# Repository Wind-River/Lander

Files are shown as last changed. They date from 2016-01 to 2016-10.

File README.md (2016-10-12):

### Overview

We will present a physical interactive model of the famous LEM Lander game, where the user attempts to land a Rocket model (suspended from a four tower cable system) that has limited fuel onto a crater-filled lunar surface.  The game has outputs to indicate the speed, altitude, and fuel level remaining, together with light and sound effects. There will be physical controller inputs for the thrust and direction, plus controls for the game play.

### Project License

The license for this project is the Apache-2.0. Text of Apache-2.0 license and other applicable license notices can be found in the LICENSE-NOTICES.txt file in the top level directory. Each source files should include a license notice that designates the licensing terms for the respective file.

### Legal Notices

Disclaimer of Warranty / No Support: Wind River does not provide support and maintenance services for this software, under Wind River’s standard Software Support and Maintenance Agreement or otherwise. Unless required by applicable law, Wind River provides the software (and each contributor provides its contribution) on an “AS IS” BASIS, WITHOUT WARRANTIES OF ANY KIND, either express or implied, including, without limitation, any warranties of TITLE, NONINFRINGEMENT, MERCHANTABILITY, or FITNESS FOR A PARTICULAR PURPOSE. You are solely responsible for determining the appropriateness of using or redistributing the software and assume ay risks associated with your exercise of permissions under the license.

### Materials Used

 * Galileo Rev2 running the Rocket (Zephyr) OS
 * Two Arduino Coprocessors 
 * 4 Stepper Motors and Drivers 
 * I2C LCD Display
 * I2C LED Large Display
 * 2 TM1637 LED Displays
 * Audio FX Sound Board
 * Pan and Tilt mount with 2 servo motors
 * Digital RGB LED Strip
 * Arcade Joystick, Buttons, and Slider Controls
 * AC power for a power strip connection
 * An internet connection (for Helix Application Cloud)
 * W=28”, D=20”, H=24” play field

### Software Used

  * Wind River Helix Application Cloud (HAC), open registration
    * http://app.cloud.windriver.com
  * Helix Application Cloud, sample application "Grove-LCD"

#### CAD and STL

  * All STL files are located in the /cad directory
  * CAD drawings for the Lander are available at - https://cad.onshape.com/documents/7df8b4dcfbc827b905a6e076

### Installation

  * Set up a free Wind River Helix Application Cloud (HAC) account (https://app.cloud.windriver.com)
  * Download the card image for the Galileo from HAC, write it to a microSD card, and insert into the Galileo
  * Create a new "Rocket_Lander" project in HAC, using the "Grove-LCD" sample application as the base
  * Set up a Galilieo Rev2 board with the following hardware:
    * A Seeed Studio Grove base shield
    * A Seeed Studio Grove button to D3
    * A Seeed Studio Grove button to D7
    * A Seeed Studio Grove LCD module to I2C
    * An FTDI cable to your host
  * Boot the Galileo, download the "Rocket_Lander" project, and do a test run with this initial application
  * Follow the Frizting diagram to attach the remaining hardware, for example:
     * The joystick cable to A0
     * The rheostat slider to A3
     * A Seeed Studio Grove PWM splitter cable from D5 to the pan and tilt stage
     * A Seeed Studio Grove breakout cable from I2C to the Adafruit I2C LED backpack
     * A Seeed Studio Grove cable with +5v cut from I2C to each of the the satellite boards
  * Follow the Frizting diagram to construct the motor driver circuit board 
  * Add code from the "source/firmware" to the "Rocket_Lander" project
  * Add code from the "source/satelliteware/libraries" to Arduino libraries directory
  * Set up the Rocket Display Arduino board
    * Install code from the "source/satelliteware/rocket_display"
    * Attach the two Seeed Studio Grove LED displays
    * Attach the Seeed Studio Grove Chainable RGB LED
    * Attach the Adafruit sound board
  * Set up the Rocket Motor Arduino board
    * Install code from the "source/satelliteware/rocket_motor"
    * Connect to the motor driver circuit board
  * Assemble the play field with the towers, stepper motors, fish line cables, and the model rocket:
    * cut a board to 28 inches by 22 inches for the playing field
    * cut four 1/2 inch square aluminum rods to 24 inches, to be the line towers
    * 3D print the four rod/motor mounts, and install on the playing field at 24 inches by 18 inches
    * 3D print the four spool cylinders and attach to the stepper motors
    * 3D print the four line rollers, and install at the top of the four towers
    * 3D print the rocket model, or provide a desired alternative
    * cut four lenghts of fish line to be the line cable, to about 60 inches
    * attach each of the four cable lines from each of the spools to the respective rocket model corner
    * attach the pan and tilt stage
    * connect the motor driver board to the stepper motors
  * Power the system, run the full "Rocket_Lander" project from HAC, follow the play instructions on the LED display interface

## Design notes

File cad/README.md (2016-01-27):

# CAD
This section will provide all physical designed files

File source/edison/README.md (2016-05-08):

#Edison Board Set up

 * To set up the board
 ```
 configure_edison --setup
 ```
 * Copy Contents of this edision directory to /home/root on the edison board
 * Install python libraries pyserial and requests
```
pip install pyserial
pip install requests
```
 * Copy startup script to /etc/init.d/rocketLanderStart
 * Put rocketLanderStart in startup with 
 ```
update-rc.d -f rocketLanderStart defaults
 ```

 * Setup Complete

##Wifi
 * Will need to be reconfigured, atm only works at WIND 
 * configure_edison --wifi

##Bluetooth
 * Will show up as RocketLander in bluetooth list
 * Default bluetooth pin is 0505
 * Set up to start up automatically

##Arduino to Edison Serial
 * Set up to start up automatically
 * log file at /home/root/arduino_edison.log
 * User DEBUG  flag to send mock data back and forth. MEAN.io rest api call is not called.
```
 python arduino_edison.py DEBUG
 ```
 * Submit High Score Message and Reply
```
a2e:name=______,score=______;
e2a:ack;
```
 * Get HighScore Message and Reply
```
a2e:highscore?;
e2a:name=_____,score=______;
```

##Rest Api Calls
 * rocketLanderRest.py calls mean stack rest api. If host changes, change ipaddress here
 * a no args equals a get for high scorre, the first 5 is returned
 * pass a json string for submit. primary key is email address
```
    [{
        "email": "mojo3@jupiter.com",
        "lander_score": 999,
        "name": "Mojo Doggie 3",
        "phone": "555-555-5555",
        "reference": "510-749-2000"
    }]
```

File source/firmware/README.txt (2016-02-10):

1) Introduction

This is the source code for the Rocket Lander main board, the Galileo.

2) Board Bring Up

  (a) Setup the Galileo with a Grove LCD on I2C and a Grove button on D3

  (b) Get the Grove-LCD sample Helix Application running
  
This will show that Rocket is working with the miniaml I/O.

  (c1) Setup the Rocket_Lander project in Helix
  
  (c2) Add these components to the Galieo
     * A Grove button on D7
     * The joystick cable to A0
     * The slider cable to A3
     * A Grove PWM splitter cable from D5 to the pan and tilt stage
     * A Grove breakout cable from I2C to a Grove protoboard to the I2C LED backpack
     * A Grove cable with +5v cut from I2C to the satellite board 
  
  (d) Run the application. In the initial startup page, select "I/O Inputs"

The two button states and the 3 ADC inputs will be traced on the debug console, to insure that the full set up inputs are working. Push both buttons together to return to the "Init" page.

  (e) Select "Main > Test > Sanity Test" 
  
This will run the following sanity tests:
  * State table sanity
  * Square Root function unit test
  * Cable Lengths function unit test
  * Tower Stepper Counts function unit test

  (f) Select "Main > Test > Simulation"

There are several flight simulation modes, using the "Next" button select.
  * "Movement in MicroMeter": move around the game space (in microMeters)
  * "Movement in MilliMeter": move around the game space (in milliMeters)
  * "Tower Cable Lengths"   : move around and observe cable length calc
  * "Tower Motor Steps"     " move around and observe cable and stepper diffs

  (g) TBD

3) Menu Structure:

	"Init"
		"I/O Inputs Test"
		"Main"

	"Main
		"Play"
		"Options"
		"Test"

	"Options"
		"Game Z"
		"Game XYZ"
		"Game Flight"
		"Game Move"
		"Game Auto Pilot"
	"Opt Gravity"
		"Gravity Full"
		"Gravity High"
		"Gravity None"
	"Opt Fuel"
		"Fuel Normal"
		"Fuel Low"
		"Fuel Nolimit"
	"Opt Pos"
		"Position Center"
		"Position Random"

	"Test"
		"I/O Inputs"
		"Test Sanity Test"
		"Test Simulation"
			"Simulation: Movement in MicroMeter"
			"Simulation: Movement in MilliMeter"
			"Simulation: Tower Cable Lengths"
			"Simulation: Tower Motor Steps"
		"Test Tower Motors"
		"Test Calibrate"
		"Test Antennae"
		"Test LED-RGB"

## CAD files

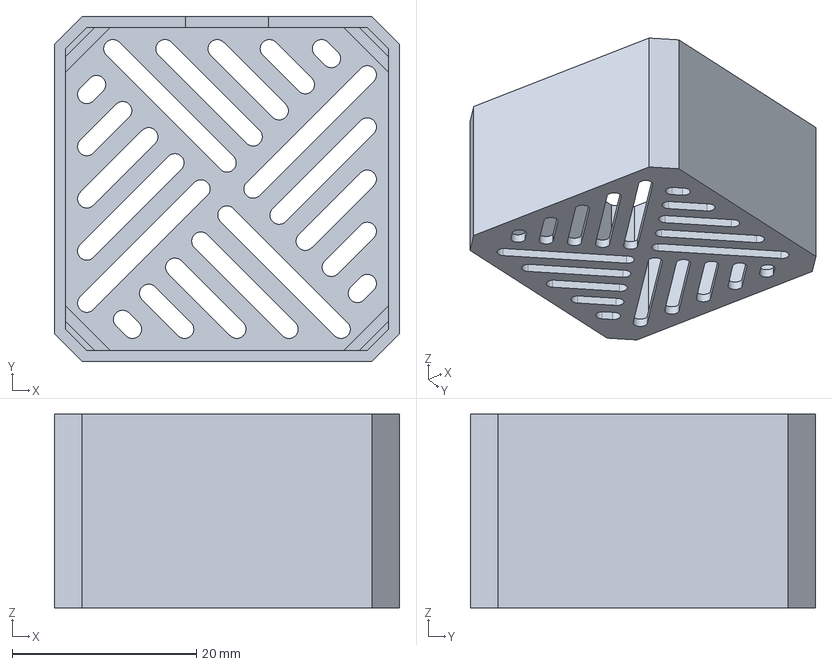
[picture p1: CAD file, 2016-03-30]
cad/Nema_14_Motor_Cover_01/Nema_14_End_Cover_01.stp
37.4 x 37.4 x 21.0 mm

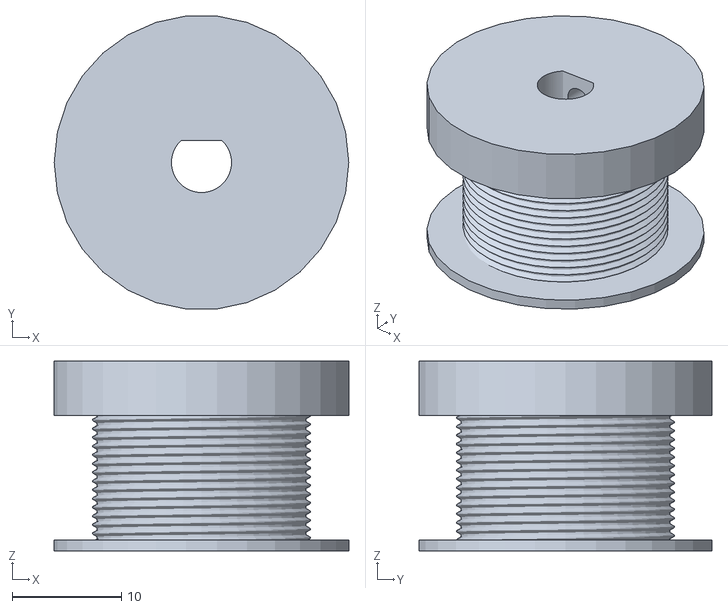
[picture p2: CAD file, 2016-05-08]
cad/stl/lander_drum275flat.stl
27.0 x 26.9 x 17.4

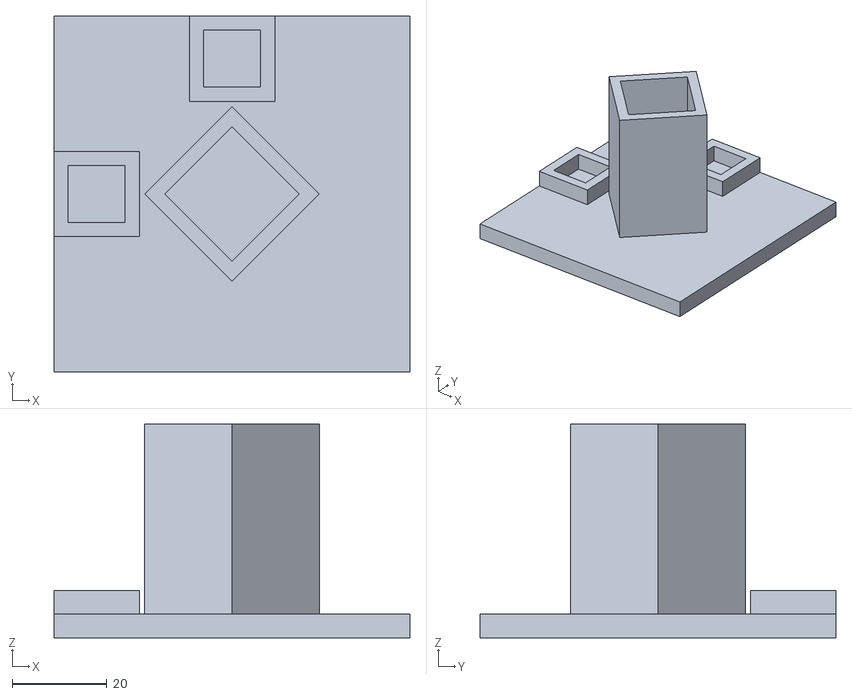
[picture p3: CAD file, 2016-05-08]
cad/stl/Lander - 2020 Footer.stl
75.0 x 75.0 x 45.0

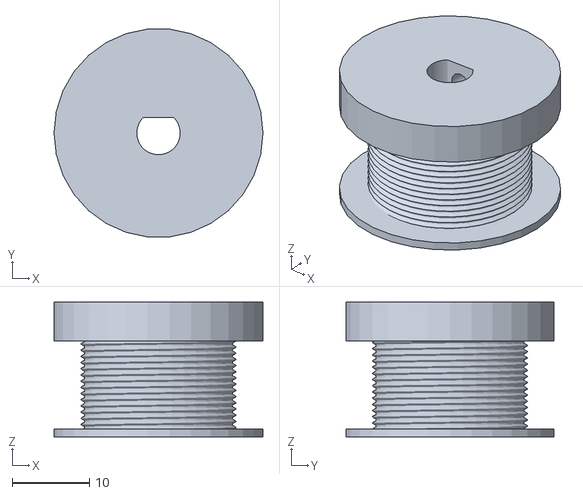
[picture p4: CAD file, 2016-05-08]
cad/stl/lander_drum28flat.stl
27.0 x 26.9 x 17.4

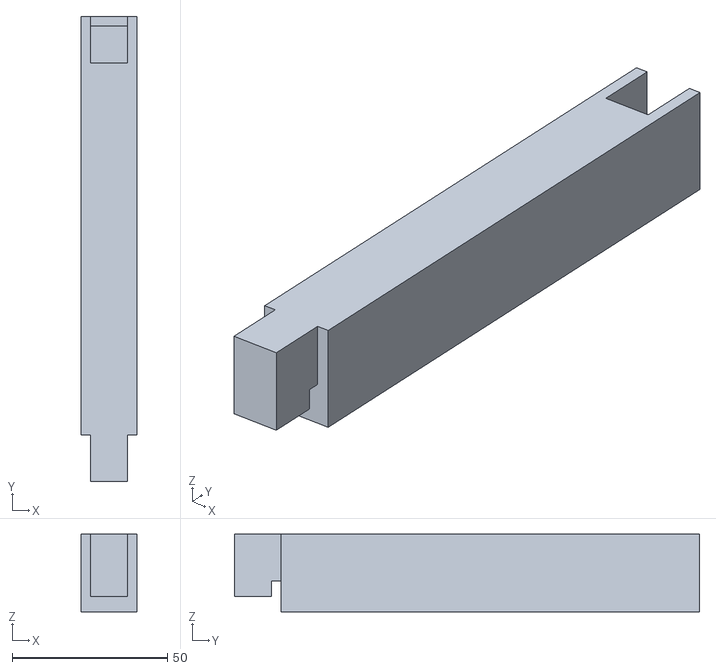
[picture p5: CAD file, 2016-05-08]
cad/stl/Lander - mf-bar.stl
18.0 x 150.0 x 25.0

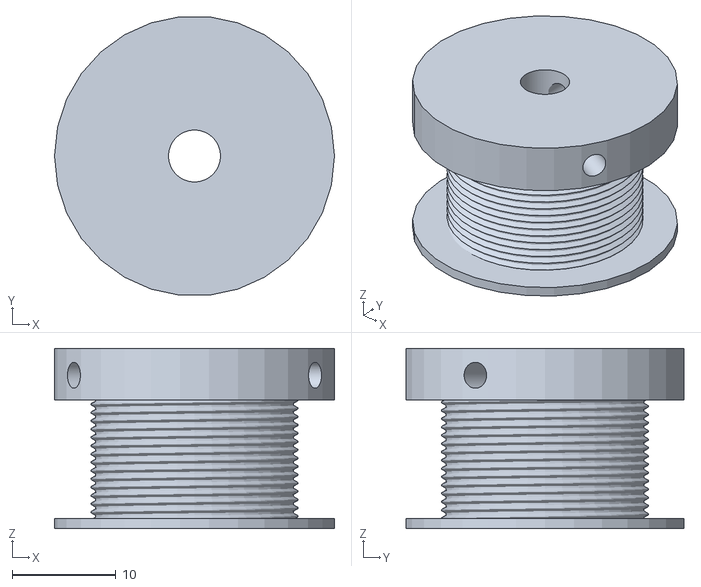
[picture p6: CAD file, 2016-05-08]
cad/stl/lander_drum.stl
27.0 x 26.9 x 17.4

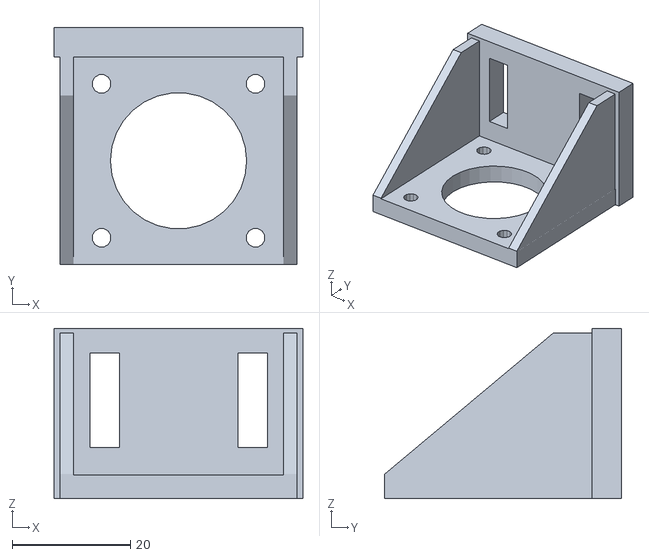
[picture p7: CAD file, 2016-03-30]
cad/stl/holder-nema-14.stl
42.1 x 40.0 x 28.8

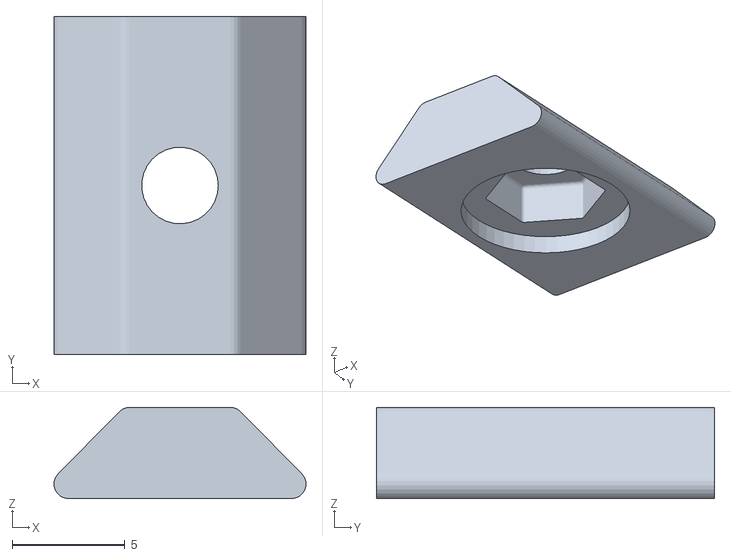
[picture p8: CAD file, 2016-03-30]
cad/stl/t-slot_insert.stl
11.2 x 15.0 x 4.05

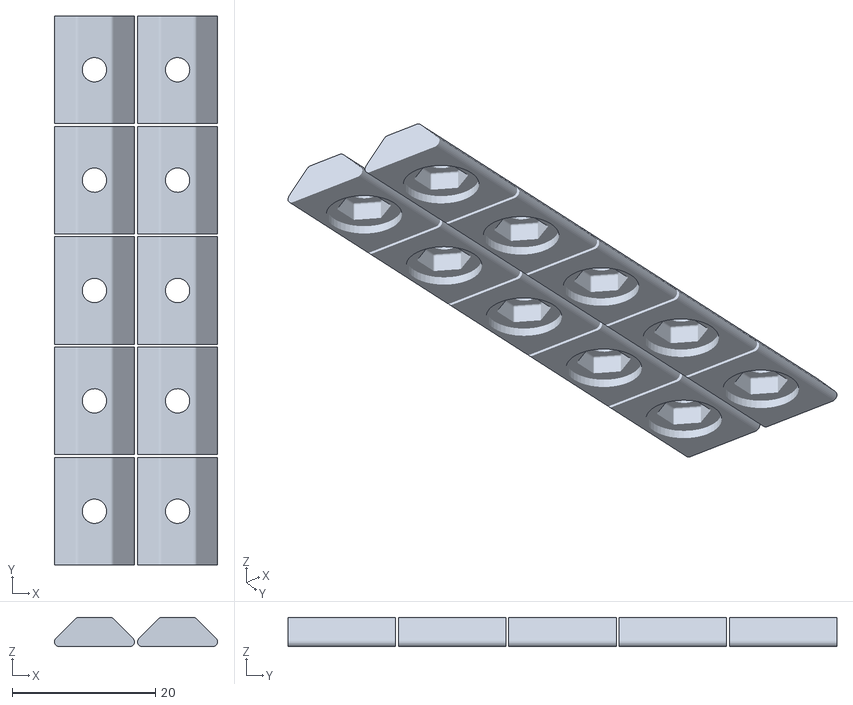
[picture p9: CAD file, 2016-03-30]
cad/stl/t-slot_insert_10pcs.stl
22.8 x 76.6 x 4.05

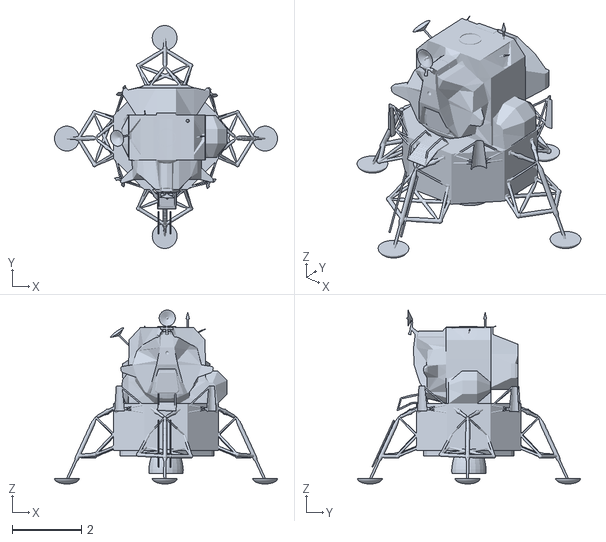
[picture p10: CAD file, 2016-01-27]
cad/stl/Lunar_Lander__fixed_.stl
6.43 x 6.43 x 5.01

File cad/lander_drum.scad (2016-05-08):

// Metric Screw Thread Library
// by Maximilian Karl <karlma@in.tum.de> (2012)
// 
//
// only use module thread(P,D,h,step)
// with the parameters:
// P    - screw thread pitch
// D    - screw thread major diameter
// h    - screw thread height
// step - step size in degree
// 
include <MCAD\polyholes.scad>

FlatShaft=true;


module screwthread_triangle(P) {
	difference() {
		translate([-sqrt(3)/3*P+sqrt(3)/2*P/8,0,0])
		rotate([90,0,0])
		cylinder(r=sqrt(3)/3*P,h=0.00001,$fn=3,center=true);

		translate([0,-P/2,-P/2])
		cube([P,P,P]);
	}
}

module screwthread_onerotation(P,D_maj,step) {
	H = sqrt(3)/2*P;
	D_min = D_maj - 5*sqrt(3)/8*P;

	for(i=[0:step:360-step])
	hull()
		for(j = [0,step])
		rotate([0,0,(i+j)])
		translate([D_maj/2,0,(i+j)/360*P])
		screwthread_triangle(P);

	translate([0,0,P/2])
	cylinder(r=D_min/2,h=2*P,$fn=360/step,center=true);
}

module thread(P,D,h,step) {
	for(i=[0:h/P])
	translate([0,0,i*P])
	screwthread_onerotation(P,D,step);
}

difference()
{
	difference()
	{
		union()
		{
			// example
			thread(0.8,20.0,12,10);
			// P    - screw thread pitch
			// D    - screw thread major diameter
			// h    - screw thread height
			// step - step size in degree
			
			translate([0,0,-0.4])
			{
				cylinder(r=13.5,h=1);
			}
			translate([0,0,12])
			{
				cylinder(r=13.5,h=5);
			}
		}
		
		translate([0,0,-0.5])
		{
			difference()
			{
				cylinder(r=2.85, h=18, $fn=100);
				//polyhole(18,5);
				if(FlatShaft)
				{
					translate([-2.5,2,-1])
					{
						cube([5,5,22]);
					}
				}
			}
		}
	}
	if(FlatShaft)
	{
		translate([0,0,14.4])
		{
			rotate([-90,90.0])
			{
				cylinder(r=1.25,h=14, $fn=100);
				//polyhole(14,2.5);
			}
		}
	}
	else
	{
		for(i = [0:120:360])
		{
			rotate([0,0,i])
			{
				translate([0,0,14.4])
				{
					rotate([-90,90.0])
					{
						cylinder(r=1.25,h=14, $fn=100);
						//polyhole(14,2.5);
					}
				}
			}
		}
	}
}

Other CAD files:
cad/stl/lander_drum285flat.stl
cad/lander_drum275.scad
cad/Nema_14_Motor_Cover_01/Nema_14_End_Cover_01.stl

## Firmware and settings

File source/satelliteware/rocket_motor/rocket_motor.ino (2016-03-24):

// rocket_motor.ino: Rocket motor mover Arduino instance

/* <legal-notice>
*
* Copyright (c) 2016 Wind River Systems, Inc.
*
* This software has been developed and/or maintained under the Wind River
* CodeSwap program. The right to copy, distribute, modify, or otherwise
* make use of this software may be licensed only pursuant to the terms
* of an applicable Wind River license agreement.
*
* <credits>
*   { David Reyna,  david.reyna@windriver.com,  },
* </credits>
*
* </legal-notice>
*/

/* rocket_motor.ino: Theory of Operation
 *
 * [Main Loop]
 *   - The main loop cycles as fast a possible, counting the micro seconds passed
 *   - Each motor has a micro second countdown timeout, at which time the next micro-step is taken
 *   - The timeout is calculalted for the number of steps needed, proportional to the longest motor move
 *   - The timeframe is nominally 1/5 second (the time between updates from the main Rocket controller)
 *   - A speed limit is enforced as per the motors, so a move may cross many timeframes
 *   - The motor is moved to low power when there is no activity via the STBY input
 *
 * [I2C Handler]
 *   - There I2C messages are received from the main Rocket controller to control motion:
 *     's' : Stop
 *     'g' : Go
 *     'p' : Preset where the rocket is now (e.g. calibration initial position from master)
 *     'd' : go to a new Destination (e.g. goto to game start location)
 *     'n' : Next move increment (e.g. joystick change)
 *     '1'..'4': send 32-bit location value to respective motor (for 'p' and 'd')
 *
 * [Serial Monitor:Debug]
 *   - Several commands are provided to do board bringup and test functionality. See 'show_help()'
 *   - The user's debug commands always run at the highest verbose level
 *   - Increase the verbose level while testing master Rocket board motor communicaton
 *
 * [Dimensions]
 *   - All stepper dimentions are in 16 bits (to conserve memory resources)
 *   - All time dimensions are in 32 bits (in micro seconds)
 *   - No long moves are done in this driver directly because of need for continual
 *     mapping of linear motion to the tower cable spherical coordinate system
 */

#include <Wire.h>
#include <inttypes.h>
#include "MicroAve.h"

#include <Stepper.h>

// General Enables
#define ENABLE_I2C      1   // Enable the I2C slave mode
#define ENABLE_TIMING   1   // enable the debug timing overhead

// setup I2C port
#define ROCKET_MOTOR_I2C_ADDRESS 19
#define I2C_READ_MAX 20

/* request read commands */
#define REQUEST_COMMAND      '?'  // set the request mode
#define REQUEST_MOVE_STATUS  's'  // return current move status as percentage completed
#define REQUEST_TIME_STATUS  't'  // return current move's remaining microseconds
#define REQUEST_SPEED_LIMIT  'l'  // return minimum micro seconds per step
#define REQUEST_POSITION     'p'  // return position

//
// which Arduino
//

#define IS_MICRO
#undef  IS_UNO

/* ======== ARDUINO MICRO PORT ASSIGNMENTS ========= */
#ifdef IS_MICRO
#define TOWER_NW_A_PORT 4
#define TOWER_NW_B_PORT 5
#define TOWER_NE_A_PORT 6
#define TOWER_NE_B_PORT 7
#define TOWER_SW_A_PORT 8
#define TOWER_SW_B_PORT 9
#define TOWER_SE_A_PORT 10
#define TOWER_SE_B_PORT 11
#define TOWER_PORT_MIN  TOWER_NW_A_PORT
#define TOWER_PORT_MAX  TOWER_SE_B_PORT
#define MOTOR_POWER_PIN 12   // power PWM output pin
#endif

/* ======== ARDUINO UNO PORT ASSIGNMENTS ========= */
#ifdef IS_UNO
#define TOWER_NW_A_PORT 3
#define TOWER_NW_B_PORT 4
#define TOWER_NE_A_PORT 5
#define TOWER_NE_B_PORT 6
#define TOWER_SW_A_PORT 7
#define TOWER_SW_B_PORT 8
#define TOWER_SE_A_PORT 9
#define TOWER_SE_B_PORT 10
#define TOWER_PORT_MIN  TOWER_NW_A_PORT
#define TOWER_PORT_MAX  TOWER_SE_B_PORT
#define MOTOR_POWER_PIN 12   // power PWM output pin
#endif

//
// Global variables
//

/* Timing objects */
MicroAve ave_i2c;
MicroAve ave_loop;
MicroAve ave_update;
MicroAve ave_latency;

/* Debugging */
#define VERBOSE_MAX 3
uint8_t verbose = 1;  // verbose level: 0=off, 1=errors,ping, 2=moves, 3=I2C
#define PING_LOOP_COUNT 10000000L // display ping every 10 seconds
#define PING_LOOP_INIT   2000000L // display first ping at 2 seconds

/* display motor positions after 3 seconds of non-activity */
#define MOVEMENT_DISPLAY_COUNT 3000000L
int32_t movement_display_counter = 0;  // coutdown pause delay

/* Request command mode */
uint8_t request_command = REQUEST_MOVE_STATUS;

//
// motor class
//

#define FRAMES_PER_SECOND        5  // 1/5 second, as per rocket control cpu
#define USECONDS_PER_FRAME 200000L  // 1/5 second
#define MOTOR_SPEED_MAX       1250  // minimum microseconds per step => maximum speed (mSec) = 240 rpm (NOTE:1000 mSec too fast for NEMA-17)
#define MOTOR_SPEED_AUTO         0  // speed is auto-calculated per frame

/* Step max: top of tower to opposite tower base
  * a = 580 mm
  * b = sqrt(480^2 + 340^2) = 588.2 mm
  * c = sqrt(580^2 + 588.2^2) = 826 mm
  * s = (826 mm * 1000 um/mm) / 125.64 uM/step = 6575 steps = 33 turns = 8 seconds
 */
#define MOTOR_DEST_MAX      6575L  // maximum step count
#define MOTOR_DEST_MIN          0  // minimum step count

/* Spindle: diameter = 8 mm, circumference = 3.141 * 8 mm = 25.128, uM/step = (25.128 * 1000)/200 = 125.64 uM/step */
#define ROCKET_TOWER_STEPS_PER_UM10  1256L  // 125.6 * 10 uMx10 per step (grab one more digit of integer math precision)
#define UM10_PER_MILLIMETER          10000L // 1000  * 10 uMx10 per millimeter

/* motor controller power */
#define MOTOR_POWER_OFF       0   // value of PWM signal to motor STBY control pins
#define MOTOR_POWER_ON      255   // STBY is full on
#define MOTOR_POWER_LOW     128   // STBY is half on
#define MOTOR_POWER_PIN_NULL  0   // power PWM output pin is undefined

/* motor mode flags */
#define MOTOR_CALIBRATE_MODE  0x01  // calibrate mode, disable step limits

class Motor {
  public:
    // constructors:
    Motor(const char * name, uint16_t pin_a,uint16_t pin_b);

    // member functions
    void step_loop(uint32_t u_sec_passed);
    void displayStatus();
    void reset();

    // static member functions
    static void move_stop();
    static void move_go();
    static void move_preset();
    static void move_destination();
    static void set_power(uint8_t request_power);
    static boolean moveRequestPending();
    static void move_next(int16_t request_inc_nw,int16_t request_inc_ne,int16_t request_inc_sw,int16_t request_inc_se,int32_t request_speed);
    static void set_next(int16_t request_set_nw,int16_t request_set_ne,int16_t request_set_sw,int16_t request_set_se,int32_t request_speed);
    static boolean motor_dispatcher(Motor *motor_nw,Motor *motor_ne,Motor *motor_sw,Motor *motor_se);

    // member variables
    const char * name;        // name of this motor's tower
    uint8_t pin_a;            // motor control A
    uint8_t pin_b;            // motor control B
    int16_t step_location;    // current location of stepper motor, in steps
    int16_t step_destination; // goal location of stepper motor, in steps
    uint32_t microseconds_step_count; // speed loop current useconds countdown
    uint32_t microseconds_per_step;   // speed loop total count, in countdown useconds

  /* error testing analytics */
    uint32_t time_step_last;    // number of microseconds since last step
    uint32_t time_step_loops;   // number of time loops since last step
    uint16_t time_step_errors;  // number of under-time step errors
    
    // static member variables
    static uint8_t power_pwm;   // power value 100=full on, 0=full off
    static uint8_t power_pin;   // pin for power control
    static uint8_t mode;        // global motor mode
    static boolean enable_motion;      // stop or go
    static boolean request_go;         // flag that a go is requested
    static boolean request_stop;       // flag that a stop is requested
    static boolean request_preset;     // flag that location is to be preset
    static boolean request_destination;// flag that destination is to be set
    static boolean request_increment;  // flag that a new incremental move is ready

    static int16_t request_increment_nw; // pending increment of stepper motor, in steps
    static int16_t request_increment_ne;
    static int16_t request_increment_sw;
    static int16_t request_increment_se;
    static int16_t request_location_nw; // pending set location of stepper motor, in steps
    static int16_t request_location_ne;
    static int16_t request_location_sw;
    static int16_t request_location_se;

    static uint32_t req_microseconds_per_step; // pending speed, in countdown useconds

    static Motor *motor_critical_path;         // which motor is the timing critical path

  private:
};

// initialize Motor static members
uint8_t Motor::power_pwm=MOTOR_POWER_OFF;
uint8_t Motor::power_pin=MOTOR_POWER_PIN_NULL;
uint8_t Motor::mode=0;
boolean Motor::request_increment;
boolean Motor::request_go;
boolean Motor::request_stop;
boolean Motor::request_preset;
boolean Motor::request_destination;
boolean Motor::enable_motion;
int16_t Motor::request_increment_nw;
int16_t Motor::request_increment_ne;
int16_t Motor::request_increment_sw;
int16_t Motor::request_increment_se;
int16_t Motor::request_location_nw;
int16_t Motor::request_location_ne;
int16_t Motor::request_location_sw;
int16_t Motor::request_location_se;
uint32_t Motor::req_microseconds_per_step;
Motor*  Motor::motor_critical_path=NULL;


Motor::Motor(const char * name, uint16_t pin_a,uint16_t pin_b) {
  this->name = name;
  this->pin_a = pin_a;
  this->pin_b = pin_b;

  // set up the motor control output pins
  pinMode(pin_a,OUTPUT);
  pinMode(pin_b,OUTPUT);

  // set the motor power pin (and preset the power off)
  if (MOTOR_POWER_PIN_NULL == power_pin) {
    power_pin = MOTOR_POWER_PIN;
    power_pwm = MOTOR_POWER_OFF;
    analogWrite(power_pin, power_pwm);
  }

  reset();
}

void Motor::reset() {
  step_location = 0L;
  step_destination = 0L;
  microseconds_step_count = 0L;
  microseconds_per_step = 0L;
  request_go = false;
  request_stop = false;
  request_increment = false;
  request_preset = false;
  request_destination = false;
  req_microseconds_per_step = 0L;
  enable_motion=true;
  time_step_last=0L;
  time_step_errors=0; 
  time_step_loops=0;
  Motor::set_power(MOTOR_POWER_OFF);
}

/* set the global motor power */
void Motor::set_power(uint8_t request_power) {
  if ((power_pwm != request_power) && (MOTOR_POWER_PIN_NULL != power_pin)) {
    power_pwm=request_power;
    analogWrite(power_pin, power_pwm);
  }
}

/* cancel any pending motion */
void Motor::move_stop() {
  request_stop = true;
}

/* start/resume any pending motion */
void Motor::move_go() {
  request_go = true;
}

/* preset current location and destination to specific value */
void Motor::move_preset() {
  request_preset = true;
}

/* move current destination to specific value */
void Motor::move_destination() {
  request_destination = true;
}


void Motor::move_next(int16_t request_inc_nw,int16_t request_inc_ne,int16_t request_inc_sw,int16_t request_inc_se,int32_t request_speed) {

  request_increment_nw = request_inc_nw;
  request_increment_ne = request_inc_ne;
  request_increment_sw = request_inc_sw;
  request_increment_se = request_inc_se;
  req_microseconds_per_step = (uint32_t) request_speed;
  request_increment = true;

  if (verbose > 1) {
    Serial.print("Move_Next=");
    Serial.print(request_inc_nw);
    Serial.print(",");
    Serial.print(request_inc_ne);
    Serial.print(",");
    Serial.print(request_inc_sw);
    Serial.print(",");
    Serial.print(request_inc_se);
    Serial.print(",Speed=");
    if (request_speed == MOTOR_SPEED_AUTO)
      Serial.println("auto");
    else
      Serial.println(request_speed);
  }

}

void Motor::set_next(int16_t request_set_nw,int16_t request_set_ne,int16_t request_set_sw,int16_t request_set_se,int32_t request_speed) {

  request_location_nw = request_set_nw;
  request_location_ne = request_set_ne;
  request_location_sw = request_set_sw;
  request_location_se = request_set_se;

  /* the respective 'preset' or 'move' command request will come is a susequent call */

  if (verbose > 1) {
    Serial.print("Set_Next=");
    Serial.print(request_set_nw);
    Serial.print(",");
    Serial.print(request_set_ne);
    Serial.print(",");
    Serial.print(request_set_sw);
    Serial.print(",");
    Serial.print(request_set_se);
    Serial.print(",Speed=");
    if (request_speed == MOTOR_SPEED_AUTO)
      Serial.println("auto");
    else
      Serial.println(request_speed);
  }
}
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
void loop() {
  uint32_t usec_now;
  uint32_t usec_diff;
  uint8_t verbose_orig = verbose;
  boolean quick_display = false;

  if (ENABLE_TIMING) ave_loop.setStop();

  // get the current time
  usec_now = micros();

  // Handle any pending move change requests
  if (Motor::motor_dispatcher(&motor_nw,&motor_ne,&motor_sw,&motor_se)) {
    /* there was a change, restart timer and wait this turn out */
    usec_last = usec_now;
    return;
  } else if (usec_now < usec_last) {
    /* there was a roll over, restart timer and wait this turn out */
    usec_last = usec_now;
    return;
  }
  usec_diff = usec_now - usec_last;
  usec_last = usec_now;

  // advance the individual motor states
  motor_nw.step_loop(usec_diff);
  motor_ne.step_loop(usec_diff);
  motor_sw.step_loop(usec_diff);
  motor_se.step_loop(usec_diff);

  // is there a debug request?
  if (Serial.available()) {
    char char_in=char(Serial.read());

    // always use maximum verbose for debug commands
    verbose=VERBOSE_MAX;

    if ('d' == char_in) {
      display_debug();
    }

    if ('H' == char_in) {
      Serial.println("");
      Serial.println("=== HISTOGRAMS ============");
      display_debug_histograms();
    }
    
    if ('r' == char_in) {
      motor_nw.reset();
      motor_ne.reset();
      motor_sw.reset();
      motor_se.reset();
      ave_i2c.reset();
      ave_loop.reset();
      ave_update.reset();
      ave_latency.reset();
    }

    // move the motors forward one step
    if ('+' == char_in) {
      motor_nw.step_destination++;
      motor_ne.step_destination++;
      motor_sw.step_destination++;
      motor_se.step_destination++;
      quick_display = true;
    }

    // move the motors back one step
    if ('-' == char_in) {
      motor_nw.step_destination--;
      motor_ne.step_destination--;
      motor_sw.step_destination--;
      motor_se.step_destination--;
      quick_display = true;
    }

    if (quick_display) {
      Serial.print("== Quick step display: NW=");
      Serial.print(motor_nw.step_destination);
      Serial.print(", NE=");
      Serial.print(motor_ne.step_destination);
      Serial.print(", SW=");
      Serial.print(motor_sw.step_destination);
      Serial.print(", SE=");
      Serial.println(motor_se.step_destination);
    }

    // move the motors forward one revolution
    if ('f' == char_in) {
      Motor::move_next(200,200,200,200,MOTOR_SPEED_AUTO);
    }

    // move the motors back one revolution
    if ('b' == char_in) {
      Motor::move_next(-200,-200,-200,-200,MOTOR_SPEED_AUTO);
    }

    // move the motors forward one revolution
    if ('1' == char_in) {
      Motor::move_next(100,100,100,100,10000);
    }

    // move the motors forward one revolution
    if ('2' == char_in) {
      Motor::move_next(100,100,100,100,20000);
    }

    // move the motors forward one revolution
    if ('3' == char_in) {
      Motor::move_next(200,200,200,200,5000);
    }

    // move the motors forward one revolution
    if ('4' == char_in) {
      Motor::move_next(200,200,200,200,2500);
    }

    // move the motors forward one revolution
    if ('5' == char_in) {
      Motor::move_next(200,200,200,200,1250);
    }

    // move the motors forward one revolution
    if ('6' == char_in) {
      Motor::move_next(200,200,200,200,1000); // 1000 too fast!
    }

    // toggle the move limit mode
    if ('m' == char_in) {
      Motor::mode ^= MOTOR_CALIBRATE_MODE;
      Serial.print("** Mode = ");
      Serial.println(Motor::mode);
    }

    // increase the standby power
    if ('p' == char_in) {
      if (Motor::power_pwm > 255-16) Motor::power_pwm = 255-16;
      Motor::set_power(Motor::power_pwm + 16);
      if (0 < verbose) {
        Serial.print("** Power = ");
        Serial.println(Motor::power_pwm);
      }
    }
    // decrease the standby power
    if ('P' == char_in) {
      if (Motor::power_pwm < 16) Motor::power_pwm = 16;
      Motor::set_power(Motor::power_pwm - 16);
      if (0 < verbose) {
        Serial.print("** Power = ");
        Serial.println(Motor::power_pwm);
      }
    }

    // goto high position
    if ('h' == char_in) {
      // ((240,170,580) to (0,0,480) (mm) = 310.6 mm = (310644 um / 125.6 um_per_step) = 2473.3 steps
      uint32_t destination = 2473;
      Motor::set_next(destination,destination,destination,destination,MOTOR_SPEED_AUTO);
      Motor::move_destination();
    }

    // goto low position
    if ('l' == char_in) {
      // ((240,170,580) to (0,0,0) (mm) = 554.7 mm = (554700 um / 125.6 um_per_step) = 4416.4 steps
      uint32_t destination = 4416;
      Motor::set_next(destination,destination,destination,destination,MOTOR_SPEED_AUTO);
      Motor::move_destination();
    }

    /* NOTE: 4416 - 2473 = 1943 steps @ 800 steps/second = 2.5 seconds move = 9.7 turns */

      // goto high NW corner position
    if ('6' == char_in) {
      Motor::set_next(
        dist2steps(-240, 170,580, -200,100,200),
        dist2steps( 240, 170,580, -200,100,200),
        dist2steps(-240,-170,580, -200,100,200),
        dist2steps( 240,-170,580, -200,100,200),
        MOTOR_SPEED_AUTO);
      Motor::move_destination();
    }
    // goto low SE corner position
    if ('7' == char_in) {
      Motor::set_next(
        dist2steps(-240, 170,580, 200,-100,0),
        dist2steps( 240, 170,580, 200,-100,0),
        dist2steps(-240,-170,580, 200,-100,0),
        dist2steps( 240,-170,580, 200,-100,0),
        MOTOR_SPEED_AUTO);
      Motor::move_destination();
    }

  // test available integer types
    if ('y' == char_in) {
      uint8_t my_byte= 1;
      uint16_t my_long= 1;
      uint32_t my_dlong= 1;
      for (int i=0;i<32;i++) {
        Serial.print(i);
        Serial.print(":");
        Serial.print(my_byte,HEX);
        Serial.print(",");
        Serial.print(my_long,HEX);
        Serial.print(",");
        Serial.println(my_dlong,HEX);
        my_byte <<= 1;
        my_long <<= 1;
        my_dlong <<= 1;
      }
    }

    if ('?' == char_in) {
      show_help();
    }

    // restore verbose level
    verbose=verbose_orig;

    if ('v' == char_in) {
      if (++verbose > VERBOSE_MAX) verbose=0;
      Serial.print("** Verbose = ");
      Serial.println(verbose);
    }
  }

  // update every 10 seconds
  if (0 < verbose) {
    loop_count -= (int32_t) usec_diff;
    if (0L >= loop_count) {
      loop_count=PING_LOOP_COUNT;
      if (1L == ping_count) show_help();
      Serial.print("ping:");
      Serial.println(ping_count);
      ping_count++;
    }
  }

  // show status of recent activity
  if (movement_display_counter) {
    movement_display_counter -= (int32_t) usec_diff;
    if (0L >= movement_display_counter) {
      movement_display_counter=0L;
      
      // set the motors to low power
      Motor::set_power(MOTOR_POWER_OFF /* MOTOR_POWER_LOW */);

      if (verbose > 0) {
        // show steps
        Serial.print("\n== Current: NW=");
        Serial.print(motor_nw.step_location);
        Serial.print(", NE=");
        Serial.print(motor_ne.step_location);
        Serial.print(", SW=");
        Serial.print(motor_sw.step_location);
        Serial.print(", SE=");
        Serial.println(motor_se.step_location);
        // show approximate millimeters
        Serial.print("        ~mm:NW=");
        Serial.print((motor_nw.step_location * ROCKET_TOWER_STEPS_PER_UM10)/UM10_PER_MILLIMETER);
        Serial.print(", NE=");
        Serial.print((motor_ne.step_location * ROCKET_TOWER_STEPS_PER_UM10)/UM10_PER_MILLIMETER);
        Serial.print(", SW=");
        Serial.print((motor_sw.step_location * ROCKET_TOWER_STEPS_PER_UM10)/UM10_PER_MILLIMETER);
        Serial.print(", SE=");
        Serial.print((motor_se.step_location * ROCKET_TOWER_STEPS_PER_UM10)/UM10_PER_MILLIMETER);
    Serial.print(", diff=");
    Serial.println(usec_diff);
        
      }
    }
  }

  if (ENABLE_TIMING) ave_loop.setStart();
}

/* user debug status dump display */
void display_debug() {
  Serial.println("\nBoard status...");

  // Motor status
  motor_nw.displayStatus();
  motor_ne.displayStatus();
  motor_sw.displayStatus();
  motor_se.displayStatus();

  // power status and mode
  Serial.print("Power = ");
  Serial.print(motor_nw.power_pwm);
  Serial.print(", Mode = ");
  Serial.println(Motor::mode);
}

void display_debug_histograms() {
  // display timing summaries
  if (ENABLE_TIMING) {
    ave_loop.displayResults("loop",true);
    //ave_i2c.displayResults("i2c",true);
  }
  ave_update.displayResults("Inc_loop",false);
  ave_latency.displayResults("Latency",true);
}

//
// Receive event from Wire's I2C master
//
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

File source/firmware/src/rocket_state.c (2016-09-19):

/* rocket_state.c - Rocket Lander Game */

/*
 *  Copyright (c) 2016 Wind River Systems, Inc.
 *
 * Licensed under the Apache License, Version 2.0 (the "License");
 * you may not use this file except in compliance with the License.
 * You may obtain a copy of the License at:
 *       http://www.apache.org/licenses/LICENSE-2.0
 *
 * Unless required by applicable law or agreed to in writing, software
 * distributed under the License is distributed on an "AS IS" BASIS,
 * WITHOUT WARRANTIES OR CONDITIONS OF ANY KIND, either express or implied.
 */

/*
 * <credits>
 *   { David Reyna,  david.reyna@windriver.com,  },
 * </credits>
 */

/*
 * Theory of Implementation
 *  - This is the state machine management system
 *  - It manages one 16x2 LCD
 *  - It uses two user buttons (expandable)
 *  - The left button (Red) is to 'stop' or go to 'next'
 *  - the right button (Green) is to 'go' or to 'select'
 *  - Each state:
 *    - Describes the display content
 *    - Describes the next state for each button press
 *    - Links the callbacks for (a) state entry, (b) state loop, (c) state exit
 *  - The sanity test validates the content of the state table
 */

#include <zephyr.h>

#include <i2c.h>
#include "groveLCDUtils.h"
#include "Adafruit_LEDBackpack.h"
#include "groveLCD.h"

#include <string.h>
#include <stdlib.h>
#include <stdbool.h>

#include "rocket.h"
#include "rocket_space.h"
#include "rocket_state.h"
#include "rocket_math.h"


/*
 * State Management
 *
 */


static uint32_t StateGuiCount=0;
static char buffer[1000];

#define StateGuiMax 160
struct StateGuiRec state_array[StateGuiMax];
int32_t state_now=0;	// current state
char * state_next_frame=NULL;	// optional state next loop
static int32_t  state_prev;	// Previous state name (for pause/resume)

static void display_state();
static int32_t find_state(char *select_state);

static int16_t state_depth=0;

char highest_name[20] = "<none>";
int16_t highest_score = 0;

// Constructor
static void StateGuiAdd(char *state_name,uint32_t flags,char *display_1,char *display_2,char *k1,char *k2,void (*state_enter)(),void (*state_loop)(),void (*state_exit)()) {
	if (StateGuiCount >= StateGuiMax) {
		log("ERROR: OUT OF STATE RECORD SPACE");
		return;
	}

	if (STATE_NOT_FOUND != find_state(state_name)) {
		log("\n");
		log_val("ERROR: Duplicate state %s\n",state_name);
		log("\n");
		/* return; keep this state so that it is visible to state unit test */
	}


	state_array[StateGuiCount].state_name = state_name;		// String name of state
	state_array[StateGuiCount].state_flags = flags;			// Optional state flags
	strcpy(state_array[StateGuiCount].display_1,display_1); 	// Display string Line 1 (16 chars) (empty string for no change)
	strcpy(state_array[StateGuiCount].display_2,display_2); 	// Display string Line 2 (16 chars)
	state_array[StateGuiCount].k1 = k1;						// Key1 goto state name (Use <STATE_NOP> for no action)
	state_array[StateGuiCount].k2 = k2;						// Key2 goto state name
	state_array[StateGuiCount].state_enter = state_enter;	// Callback on state entry (Use <ACTION_NOP> for no action)
	state_array[StateGuiCount].state_loop  = state_loop;	// Callback on state loop
	state_array[StateGuiCount].state_exit  = state_exit;	// Callback on state exit
	StateGuiCount++;
}

void set_lcd_display(int32_t line,char *buffer) {
	if (LCD_BUFFER_1 == line) {
		strncpy(state_array[state_now].display_1,buffer,LCD_DISPLAY_POS_MAX);
		state_array[state_now].display_1[LCD_DISPLAY_POS_MAX]='\0';
	}
	if (LCD_BUFFER_2 == line) {
		strncpy(state_array[state_now].display_2,buffer,LCD_DISPLAY_POS_MAX);
		state_array[state_now].display_2[LCD_DISPLAY_POS_MAX]='\0';
	}
}

static void display_state() {
	char *display_1 = state_array[state_now].display_1;
	char *display_2 = state_array[state_now].display_2;

	// protect the display length
	state_array[state_now].display_1[LCD_DISPLAY_POS_MAX]='\0';
	state_array[state_now].display_2[LCD_DISPLAY_POS_MAX]='\0';

	// check if inherited state
	if (0 == strcmp(STATE_INHERIT_S,display_1))
		display_1 = state_array[state_prev].display_1;
	if (0 == strcmp(STATE_INHERIT_S,display_2))
		display_2 = state_array[state_prev].display_2;

	if (0 < strlen(display_1)) {
		// pad if not empty
		sprintf(r_control.lcd_line0,"%-16s",display_1);
	} else {
		display_1[0] = '\0';
	}

	if (0 < strlen(display_2))
		// pad and/or reverse if not empty
		if (STATE_REVERSE_MENUS) {
			// flip the menu labels,
			// Case 1: two strings separated by spaces (normal)
			// Case 2: one string on left
			// Case 3: one string on right
			// Case 4: one long string
			// Case 5: no strings, just spaces (e.g. pass through states)
			uint8_t first_space=0,last_space=15,i;

			for (i=0;i<=32;i++) buffer[i]=' ';
			sprintf(&buffer[16],"%-16s",display_2);

			while ((' ' != buffer[16+first_space]) && (first_space<16)) first_space++;
			while ((' ' != buffer[16+last_space ]) && (last_space > 0)) last_space--;

			if (first_space > 0)
				strncpy(&buffer[16-first_space],&buffer[16],first_space);

			if ((last_space < 15) && (last_space >= first_space))
				strncpy(buffer,&buffer[16+last_space+1],15-last_space);

			if (first_space < last_space)
				strncpy(&buffer[15-last_space],&buffer[16+first_space],last_space-first_space+1);

			buffer[16]='\0';
			strcpy(r_control.lcd_line1,buffer);
		} else {
			sprintf(r_control.lcd_line1,"%-16s",display_2);
		}
	else {
		display_2[0] = '\0';
	}

	if (verbose && (0x0000 == (state_array[state_now].state_flags & STATE_NO_VERBOSE))) {
		log("\n");
		sprintf(buffer,"/----------------\\ State=%s, Depth=%d\n",state_array[state_now].state_name,state_depth);
		log(buffer);
		sprintf(buffer,"|%s|\n",r_control.lcd_line0);
		log(buffer);
		sprintf(buffer,"|%s|\n",r_control.lcd_line1);
		log(buffer);
		log("\\----------------/\n");
		sprintf(buffer,"1:=%s, 2=%s\n",
			(STATE_NOP == state_array[state_now].k1)?"None":state_array[state_now].k1,
			(STATE_NOP == state_array[state_now].k2)?"None":state_array[state_now].k2);
		log(buffer);
	}

	// Send text to screen
	if (IO_LCD_ENABLE) {
		if (strlen(r_control.lcd_line0)) groveLcdPrint(i2c, 0, 0, r_control.lcd_line0, strlen(r_control.lcd_line0));
		if (strlen(r_control.lcd_line1)) groveLcdPrint(i2c, 1, 0, r_control.lcd_line1, strlen(r_control.lcd_line1));
	}
}

static int32_t find_state(char *select_state) {
	int32_t i;
	if (STATE_NOP == select_state)
		return STATE_NOT_FOUND;
	for (i=0;i<StateGuiMax;i++) {
		if (0 == strcmp(select_state,state_array[i].state_name))
			return i;
	}
	return STATE_NOT_FOUND;
}
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

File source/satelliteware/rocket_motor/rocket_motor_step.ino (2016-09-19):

// rocket_motor.ino: Rocket motor mover Arduino instance

/*
 *  Copyright (c) 2016 Wind River Systems, Inc.
 *
 * Licensed under the Apache License, Version 2.0 (the "License");
 * you may not use this file except in compliance with the License.
 * You may obtain a copy of the License at:
 *       http://www.apache.org/licenses/LICENSE-2.0
 *
 * Unless required by applicable law or agreed to in writing, software
 * distributed under the License is distributed on an "AS IS" BASIS,
 * WITHOUT WARRANTIES OR CONDITIONS OF ANY KIND, either express or implied.
 */

/*
 * <credits>
 *   { David Reyna,  david.reyna@windriver.com,  },
 * </credits>
 *
 */

/* rocket_motor.ino: Theory of Operation
 *
 * 1) There is a tack of dir/step stepper controllers (e.g. Pololu DRV8834)
 *        4 are for the rocket tower (e.g. Pololu Bipolar, 200 Steps/Rev, 7.2v)
 *    9..12 are for the surface (e.g. S20M024S03-M7, 24 step 5 V)
 *    
 * 2) Here are the data controls
 *   (a) One control for all motors DIR input
 *   (b) Four bit select to 2x74LS138 muxes for controller STEP input
 *   (c) Same four bit select to 2x74LS151 demuxes for motor boundary switch 
 *   (d) One enable bit for the 74LS138 muxes, when the selects are stable
 *   (e) One control for all motors SLEEP input
 *   (f) One input control for all motors SLEEP input
 *   
 * 3) Main Loop
 *   - The main loop cycles as fast a possible, counting the micro seconds passed
 *   - Each motor has a micro second countdown timeout, at which time the next micro-step is taken
 *   - The timeout is calculalted for the number of steps needed, proportional to the longest motor move
 *   - The timeframe is nominally 1/5 second (the time between updates from the main Rocket controller)
 *   - A speed limit is enforced as per the motors, so a move may cross many timeframes
 *   - The motors are moved to full power when any move command is received
 *   - The motors are moved to SLEEP/STBY after 2 seconds when there is no activity
 *   
 * 4) Stepping for a given motor
 *   (a) the DIR motor bit is set
 *   (b) the 4 select bits are set
 *   (c) motor boundary input tested, if triggered motion is stopped
 *   (d) the select enable set is set, triggering the respective STEP motor bit
 *   (e) the select enable set is unset after 2 mSec
 *   
 * 5) I2C Handler
 *   - There I2C messages are received from the main Rocket controller to control motion:
 *     'S' : Stop
 *     'P' : Preset where the rocket is now (e.g. calibration initial position from master)
 *     'D' : go to a new Destination (e.g. goto to game start location)
 *     'I' : Next move increment (e.g. joystick change)
 *     '0'..'c': send 32-bit location value to respective motor (for 'p' and 'd')
 *
 * 6) Serial Monitor:Debug
 *   - Several commands are provided to do board bringup and test functionality. See 'show_help()'
 *   - The user's debug commands always run at the highest verbose level
 *   - Increase the verbose level while testing master Rocket board motor communicaton
 *
 * 7) Dimensions
 *   - All stepper dimentions are in 16 bits (to conserve memory resources)
 *   - All time dimensions are in 32 bits (in micro seconds)
 *   - No long moves are done in this driver directly because of need for continual
 *     mapping of linear motion to the tower cable spherical coordinate system
 */

#include <Wire.h>
#include <inttypes.h>
#include "MicroAve.h"

#include <Stepper.h>

// General Enables
#define ENABLE_I2C      1   // Enable the I2C slave mode

#define ENABLE_MEASURE_LOOP     1 // measure main loop time
#define ENABLE_MEASURE_I2C      0 // measure I2C processing time
#define ENABLE_MEASURE_UPDATE   0 // measure incremental movement update time
#define ENABLE_MEASURE_LATENCY  0 // measure latency for motor incement timeout versus goal

// setup I2C port
#define ROCKET_MOTOR_I2C_ADDRESS 19
#define I2C_READ_MAX 20

/* request write commands */
#define REQUEST_STOP         's'  // send stop
#define REQUEST_PRESET       'p'  // send preset
#define REQUEST_DESTINATION  'd'  // send destination
#define REQUEST_INCREMENT    'n'  // set the request mode
#define REQUEST_ROCKET_LOC   'l'  // set the request mode

#define REQUEST_COMMAND      '?'  // set the request mode
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

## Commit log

2016-01-27 initial checkin
    [Lunar_Lander__fixed_.stl]
2016-02-05 Create prj.mdef
    Enable Rocket event for ADC converter
2016-02-09 Update main.c
    * Game display modes
    * raw x,y,z,f (mm units)
    * raw cables lengths (mm)
    * Large and small state LEDs
    * Vincent's I2C code for large display, I2C adapter
    * small LEDs
    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
2016-02-09 Update rocket.h
    * Communication with daughter Arduino
    * daughter I2C connection
    * daughter client
    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
2016-02-09 Update rocket_state.c
    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
2016-02-19 Added files via upload
    Add the Rocket Display manager Arduino code
2016-02-19 Create rocket_motor.ino
    Controller code for Rocket motor controller Arduino
2016-02-19 fix verbose flag type and range
    [rocket_display.ino]
2016-02-20 first pass run test fixes
    [rocket_motor.ino]
2016-02-20 add rocket motor board increment send
2016-02-20 updated I2C port names
2016-02-20 add rocket motor board increment send test
2016-02-24 fix mm to step conversion
    [rocket_space.h]
2016-02-26 fix speed limit, step computation
    [rocket_motor.ino]
2016-02-29 fix step timing, add power control
    [rocket_motor.ino]
2016-02-29 set tower positions, rocket mount points
2016-03-01 add i2c position request, reset game dimensions
    [rocket_motor.ino]
2016-03-01 fix rocket mount parameters
    [rocket_space.h]
2016-03-01 protect square root loops, fix GAME_AT_HOME position set
    [rocket_space.c]
2016-03-02 fix scale constants from cm to mm
    [rocket_space.h]
2016-03-05 add calibrate mode
2016-03-05 add calibration motor lock
2016-03-05 rotate rocket mount, temp remove home slack
2016-03-10 motor step calibration, block no-change sends
2016-03-10 motor step calibration, move sqrt to rocket_math
2016-03-10 rework button assignments red/green = next/select
    [rocket_state.c]
2016-03-16 name the frames per second, default speed
2016-03-24 add short step loop detection, fix timer types
    [rocket_motor.ino]
2016-03-24 add cable calibration table, circular flight, parameterize center
2016-03-24 fix rocket position preset, cable calculations
    [rocket_space.c]
2016-03-30 circular rotation, panic button, move to game start
2016-03-30 added STL files and link to OnShape. updated readme
    [MotorMount.stl, Nema_14_End_Cover_01.stl, Nema_14_End_Cover_01.stp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]
2016-03-31 add attract sound, enable rocket_display board
2016-03-31 fix motion at boundaries
    [rocket_space.c]
2016-04-01 add Adafruit joystick mapping, invert slider option
    [rocket.h]
2016-05-05 move directory structure aroud; update README to md format; add arduino_edison.py;
2016-05-05 committing startup file just in case
2016-05-05 Update Readme, document arduino_edison.py
2016-05-05 arduino_edison works with rest api calls add enable_serial_edison to startup
2016-05-06 fix adafruit joystick adaptor for middle pos at zero volts
    [main.c]
2016-05-06 arduino sending high score to edison
2016-05-06 Update Edision Readme on how to setup the board
2016-05-07 wrap score trace in higher verbosity setting
    Wrap the trace statements for high score in a verbosity section to protect default response time for i2c handler.
2016-05-08 updated stl files
    [Lander - 2020 Footer.stl, Lander - mf-bar.stl, MotorMount.stl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]
2016-06-07 rocket motor executive for step-based control
    This implementation of the rocket stepper motor controller manages motor controllers with step inputs (as opposed to phase inputs). This design allows one Arduino Uno/Micro/Trinket controller to easi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
2016-06-07 add checkpoints, respell "antenna"
2016-06-07 add new ground test compass
2016-06-07 add tracker, ground move support
2016-06-07 replace 'state_callback' with direct function pointers, add ground support, cleanup
    [rocket_state.c]
2016-06-07 Fritzing diagram, rev 1 (phase motor control)
    [Rocket_Lander_Rev1.fzz]
2016-06-08 fix speed calculation, add LCD speed status color
    [rocket_state.c]
2016-06-09 fix joystick map, add tracepoints
    [main.c]
2016-06-09 fix speed LED display, add LCD safety re-init
    [rocket_state.c]
